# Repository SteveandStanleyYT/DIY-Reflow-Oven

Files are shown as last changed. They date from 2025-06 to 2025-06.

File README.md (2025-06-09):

# DIY Reflow Oven
## Objective
We are going to be building a lot of SMD PCBs in the future and so we would want to invest in a reflow oven. But the current consumer reflow ovens are very expensive and also require a lot of mods to get them working well. For these reasons, we decided to build our own reflow oven. 

## Requirements
- It should be able to fit a medium-sized board.
- It should look aesthetically pleasing (Wires should not be dangling around.)

## Components
| Component | Link | 
|---|---|
| Hamilton Beach toaster oven | [Link](https://www.amazon.com/gp/product/B08CW95ZFR/ref=ewc_pr_img_1?smid=ATVPDKIKX0DER&psc=1) | 
| Panasonic Solid State relay (AQA211VL) | [AQA211VL](https://www.digikey.com/en/products/detail/panasonic-electric-works/AQA211VL/2364682) | 
| RTD PT100 Sensor | [Link](https://www.amazon.com/T-PRO-Bonded-PT100-Sensor-3-3Ft/dp/B08LM65RR9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) |  
| MAX31865 RTD Temperature Thermocouple | [Link](https://www.amazon.com/HiLetgo-MAX31865-Temperature-Thermocouple-Amplifier/dp/B071DVVZHC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) |
| Ceramic Blanket | [Link](https://www.aliexpress.us/item/3256802930270704.html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) | 
| Aluminum reflective tape | — | 
| 240×320 SPI Display | — | 
| ESP32 | — | 
| 12V 1A Power Supply | [Link](https://www.aliexpress.us/item/3256802541723599.html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) | 
| Cooling Fan | — | 
| Green LED | [Link](https://www.digikey.com/en/products/detail/lumex-opto-components-inc/SSI-LXH1090GD/144696)| 
| Red LED | [Link](https://www.digikey.com/en/products/detail/lumex-opto-components-inc/SSI-LXH1090SRD/144702)| 
| Buzzer | — |
| Switch | — | 
| Relay | — |
| Terminal Blocks | — | 
| USB-C to Micro USB cable | - |

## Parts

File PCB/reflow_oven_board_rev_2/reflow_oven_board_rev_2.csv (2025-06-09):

Source: | /Users/stevenketiah/Desktop/Personal_Projects/DIY REFLOW OVEN/Reflow_oven_board/Reflow_oven_board.kicad_sch
Date: | Wednesday, March 13, 2024 at 11:47:50 PM
Tool: | Eeschema 7.0.10
Generator: | /Applications/KiCad/KiCad.app/Contents/SharedSupport/plugins/bom_csv_grouped_by_value.py
Component Count: | 44
Collated Components:
Item | Qty | Reference(s) | Value | LibPart | Footprint | Datasheet | DNP | Availability | Check_prices | Description | MANUFACTURER | MAXIMUM_PACKAGE_HEIGHT | MF | MP | PARTREV | Package | Price | STANDARD | SnapEDA_Link
1 | 1 | BZ1 | Buzzer | Device:Buzzer | Buzzer_Beeper:Buzzer_12x9.5RM7.6 | ~
2 | 1 | C1 | 10u | Device:C | Capacitor_SMD:C_0603_1608Metric_Pad1.08x0.95mm_HandSolder | ~
3 | 3 | C2, C3, C7 | 0.1u | Device:C | Capacitor_SMD:C_0603_1608Metric_Pad1.08x0.95mm_HandSolder | ~
4 | 2 | C4, C5 | 22u | Device:C | Capacitor_SMD:C_0603_1608Metric_Pad1.08x0.95mm_HandSolder | ~
5 | 1 | C6 | 56p | Device:C | Capacitor_SMD:C_0603_1608Metric_Pad1.08x0.95mm_HandSolder | ~
6 | 1 | C8 | 10nF | Device:C | Capacitor_SMD:C_0603_1608Metric_Pad1.08x0.95mm_HandSolder | ~
7 | 1 | J1 | ~ | Connector:Conn_01x14_Socket | Connector_PinSocket_2.54mm:PinSocket_1x14_P2.54mm_Vertical | ~
8 | 6 | J2, J3, J4, J5, J6, J7 | ~ | Connector:Screw_Terminal_01x02 | TerminalBlock_Phoenix:TerminalBlock_Phoenix_MKDS-1,5-2_1x02_P5.00mm_Horizontal | ~
9 | 1 | J8 | Screw_Terminal_01x03 | Connector:Screw_Terminal_01x03 | TerminalBlock_Phoenix:TerminalBlock_Phoenix_MKDS-1,5-3_1x03_P5.00mm_Horizontal | ~
10 | 1 | L1 | 15u | Device:L | Inductor_SMD:L_Taiyo-Yuden_NR-80xx_HandSoldering | ~
11 | 5 | Q1, Q2, Q3, Q4, Q5 | DMG3402L | Transistor_FET:DMG3402L | Package_TO_SOT_SMD:SOT-23 | http://www.diodes.com/assets/Datasheets/DMG3402L.pdf
12 | 1 | R1 | 510k | Device:R_US | Resistor_SMD:R_0603_1608Metric_Pad0.98x0.95mm_HandSolder | ~
13 | 5 | R2, R5, R6, R7, R14 | 150 | Device:R_US | Resistor_SMD:R_0603_1608Metric_Pad0.98x0.95mm_HandSolder | ~
14 | 1 | R3 | 100k | Device:R_US | Resistor_SMD:R_0603_1608Metric_Pad0.98x0.95mm_HandSolder | ~
15 | 1 | R4 | 22.1k | Device:R_US | Resistor_SMD:R_0603_1608Metric_Pad0.98x0.95mm_HandSolder | ~
16 | 2 | R8, R9 | 60.4 | Device:R_US | Resistor_SMD:R_0603_1608Metric_Pad0.98x0.95mm_HandSolder | ~
17 | 5 | R10, R11, R12, R13, R15 | 10k | Device:R_US | Resistor_SMD:R_0603_1608Metric_Pad0.98x0.95mm_HandSolder | ~
18 | 3 | TP1, TP3, TP4 | TestPoint_Alt | Connector:TestPoint_Alt | TestPoint:TestPoint_Pad_D1.0mm | ~
19 | 1 | U1 | ESP32-DEVKIT-V1 | ESP32-DEVKIT-V1:ESP32-DEVKIT-V1 | ESP32-DEVKIT-V1:MODULE_ESP32_DEVKIT_V1 |  |  | Not in stock | https://www.snapeda.com/parts/ESP32-DEVKIT-V1/Do+it/view-part/?ref=eda | Dual core, Wi-Fi: 2.4 GHz up to 150 Mbits/s,BLE (Bluetooth Low Energy) and legacy Bluetooth, 32 bits, Up to 240 MHz | DOIT | 6.8 mm | Do it | ESP32-DEVKIT-V1 | N/A | None | None | Manufacturer Recommendations | https://www.snapeda.com/parts/ESP32-DEVKIT-V1/Do+it/view-part/?ref=snap
20 | 1 | U2 | TPS54202HDDCR | Regulator_Switching:TPS54202H | Package_TO_SOT_SMD:SOT-23-6_Handsoldering | https://www.ti.com/general/docs/suppproductinfo.tsp?distId=10
21 | 1 | U3 | MAX31855KASA | Sensor_Temperature:MAX31855KASA | Package_SO:SOIC-8_3.9x4.9mm_P1.27mm | http://datasheets.maximintegrated.com/en/ds/MAX31855.pdf

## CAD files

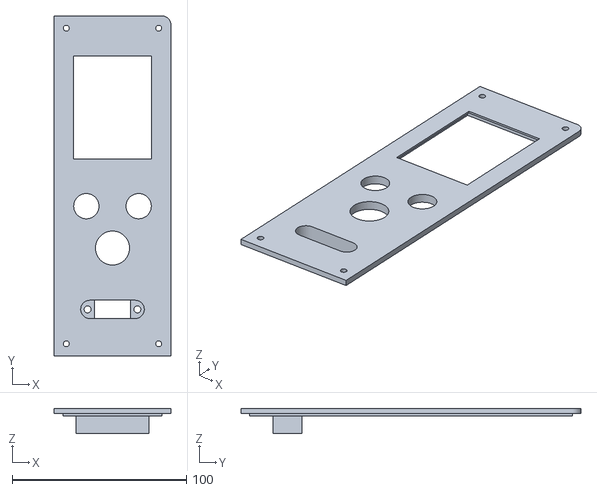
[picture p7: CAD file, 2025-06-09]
CAD/faceplate.stl
67.0 x 195.0 x 14.5

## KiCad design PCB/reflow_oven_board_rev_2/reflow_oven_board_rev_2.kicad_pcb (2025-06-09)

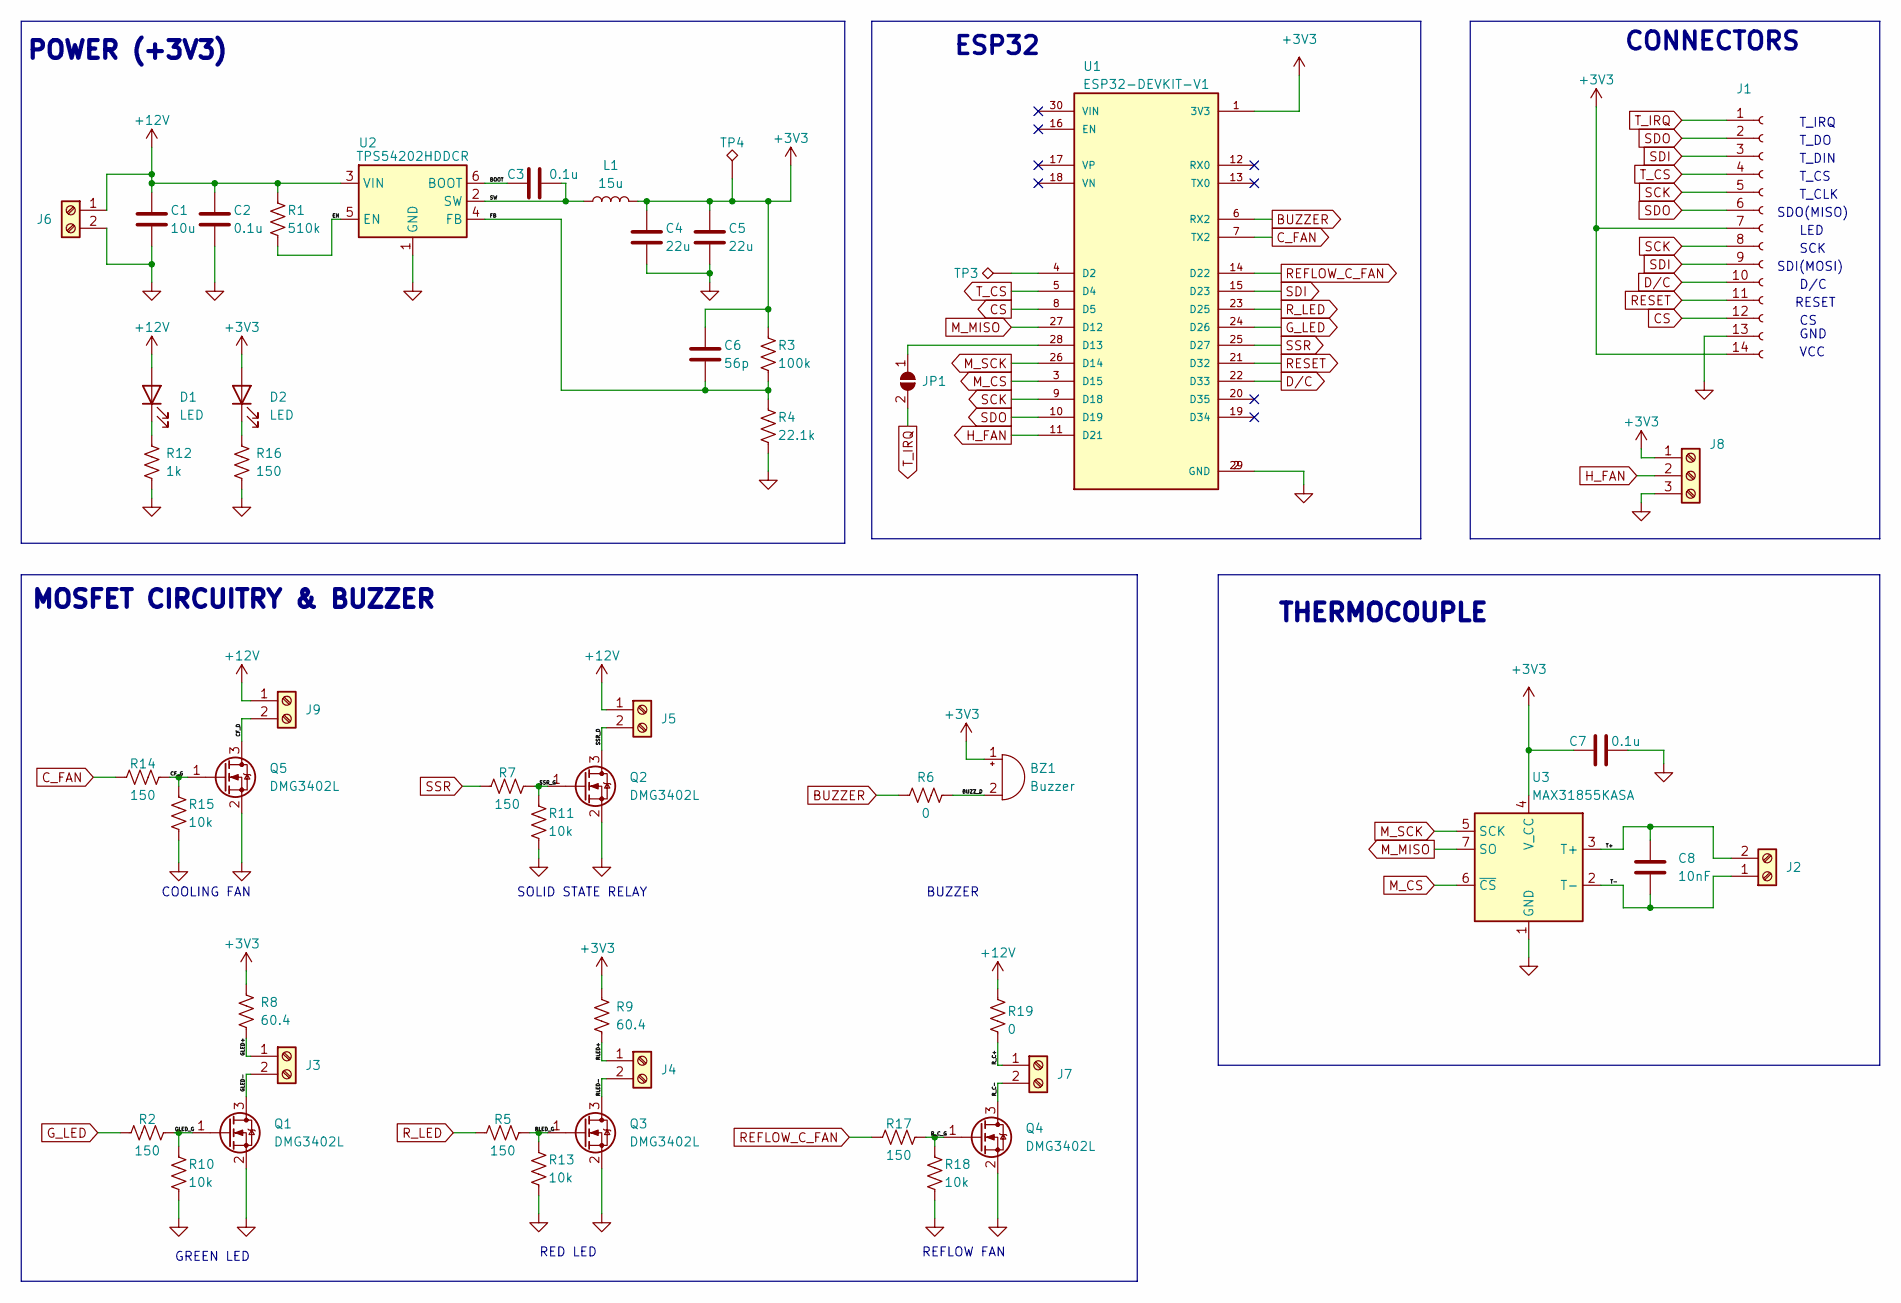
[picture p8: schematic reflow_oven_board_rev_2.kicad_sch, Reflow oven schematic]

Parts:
BZ1: Buzzer; Buzzer_12x9.5RM7.6
C1: 10u; C_0603_1608Metric_Pad1.08x0.95mm_HandSolder
C2, C3, C7: 0.1u; C_0603_1608Metric_Pad1.08x0.95mm_HandSolder
C4, C5: 22u; C_0603_1608Metric_Pad1.08x0.95mm_HandSolder
C6: 56p; C_0603_1608Metric_Pad1.08x0.95mm_HandSolder
C8: 10nF; C_0603_1608Metric_Pad1.08x0.95mm_HandSolder
D1, D2: LED; LED_0603_1608Metric
J1: PinSocket_1x14_P2.54mm_Vertical
J2, J3, J4, J5, J6, J7, J9: TerminalBlock_Phoenix_MKDS-1,5-2_1x02_P5.00mm_Horizontal
J8: Screw_Terminal_01x03; TerminalBlock_Phoenix_MKDS-1,5-3_1x03_P5.00mm_Horizontal
JP1: SolderJumper_2_Open; PinHeader_1x02_P2.54mm_Vertical
L1: 15u; L_Taiyo-Yuden_NR-80xx
Q1, Q2, Q3, Q4, Q5: DMG3402L; SOT-23
R1: 510k; R_0603_1608Metric_Pad0.98x0.95mm_HandSolder
R2, R5, R7, R14, R17: 150; R_0603_1608Metric_Pad0.98x0.95mm_HandSolder
R3: 100k; R_0603_1608Metric_Pad0.98x0.95mm_HandSolder
R4: 22.1k; R_0603_1608Metric_Pad0.98x0.95mm_HandSolder
R6: 0; R_0603_1608Metric
R8, R9: 60.4; R_0603_1608Metric_Pad0.98x0.95mm_HandSolder
R10, R11, R13, R15, R18: 10k; R_0603_1608Metric_Pad0.98x0.95mm_HandSolder
R12: 1k; R_0603_1608Metric
R16: 150; R_0603_1608Metric
R19: 0; R_0603_1608Metric_Pad0.98x0.95mm_HandSolder
TP3, TP4: TestPoint_Alt; TestPoint_Pad_D1.0mm
U1: ESP32-DEVKIT-V1; MODULE_ESP32_DEVKIT_V1; PARTREV N/A
U2: TPS54202HDDCR; SOT-23-6_Handsoldering
U3: MAX31855KASA; SOIC-8_3.9x4.9mm_P1.27mm

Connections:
+3V3: BZ1.1 (+), C4.1, C5.1, C6.1, C7.1, D2.2 (A), J1.7, J1.14, J8.1, L1.2, R3.1, R8.1, R9.1, TP4.1, U1.1 (3V3), U3.4 (V_CC)
+12V: C1.1, C2.1, D1.2 (A), J5.1, J6.1, J9.1, R1.1, R19.1, U2.3 (VIN)
/BOOT: C3.1, U2.6 (BOOT)
/BUZZ_D: BZ1.2 (-), R6.2
/CF_D: J9.2, Q5.3 (D)
/CF_G: Q5.1 (G), R14.2, R15.1
/EN: R1.2, U2.5 (EN)
/FB: C6.2, R3.2, R4.1, U2.4 (FB)
/GLED+: J3.1, R8.2
/GLED-: J3.2, Q1.3 (D)
/GLED_G: Q1.1 (G), R2.2, R10.1
/RLED+: J4.1, R9.2
/RLED-: J4.2, Q3.3 (D)
/RLED_G: Q3.1 (G), R5.2, R13.1
/R_C+: J7.1, R19.2
/R_C-: J7.2, Q4.3 (D)
/R_C_G: Q4.1 (G), R17.2, R18.1
/SSR_D: J5.2, Q2.3 (D)
/SSR_G: Q2.1 (G), R7.2, R11.1
/SW: C3.2, L1.1, U2.2 (SW)
/T+: C8.1, J2.2, U3.3 (T+)
/T-: C8.2, J2.1, U3.2 (T-)
BUZZER: R6.1, U1.6 (RX2)
CS: J1.12, U1.8 (D5)
C_FAN: R14.1, U1.7 (TX2)
D/C: J1.10, U1.22 (D33)
GND: C1.2, C2.2, C4.2, C5.2, C7.2, J1.13, J6.2, J8.3, Q1.2 (S), Q2.2 (S), Q3.2 (S), Q4.2 (S), Q5.2 (S), R4.2, R10.2, R11.2, R12.2, R13.2, R15.2, R16.2, R18.2, U1.2 (GND), U1.29 (GND), U2.1 (GND), U3.1 (GND)
G_LED: R2.1, U1.24 (D26)
H_FAN: J8.2, U1.11 (D21)
M_CS: U1.3 (D15), U3.6 (~CS)
M_MISO: U1.27 (D12), U3.7 (SO)
M_SCK: U1.26 (D14), U3.5 (SCK)
unnamed: D1.1 (K), R12.1
unnamed: D2.1 (K), R16.1
unnamed: JP1.1 (A), U1.28 (D13)
unnamed: TP3.1, U1.4 (D2)
REFLOW_C_FAN: R17.1, U1.14 (D22)
RESET: J1.11, U1.21 (D32)
R_LED: R5.1, U1.23 (D25)
SCK: J1.5, J1.8, U1.9 (D18)
SDI: J1.3, J1.9, U1.15 (D23)
SDO: J1.2, J1.6, U1.10 (D19)
SSR: R7.1, U1.25 (D27)
T_CS: J1.4, U1.5 (D4)
T_IRQ: J1.1, JP1.2 (B)

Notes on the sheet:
GREEN LED
T_CS
LED
THERMOCOUPLE
BUZZER
SOLID STATE RELAY
CONNECTORS
SDI(MOSI)
POWER (+3V3)
T_DIN
RED LED
VCC
RESET
MOSFET CIRCUITRY & BUZZER
T_IRQ
COOLING FAN
REFLOW FAN
GND
SDO(MISO)
T_DO
T_CLK
SCK
ESP32
D/C

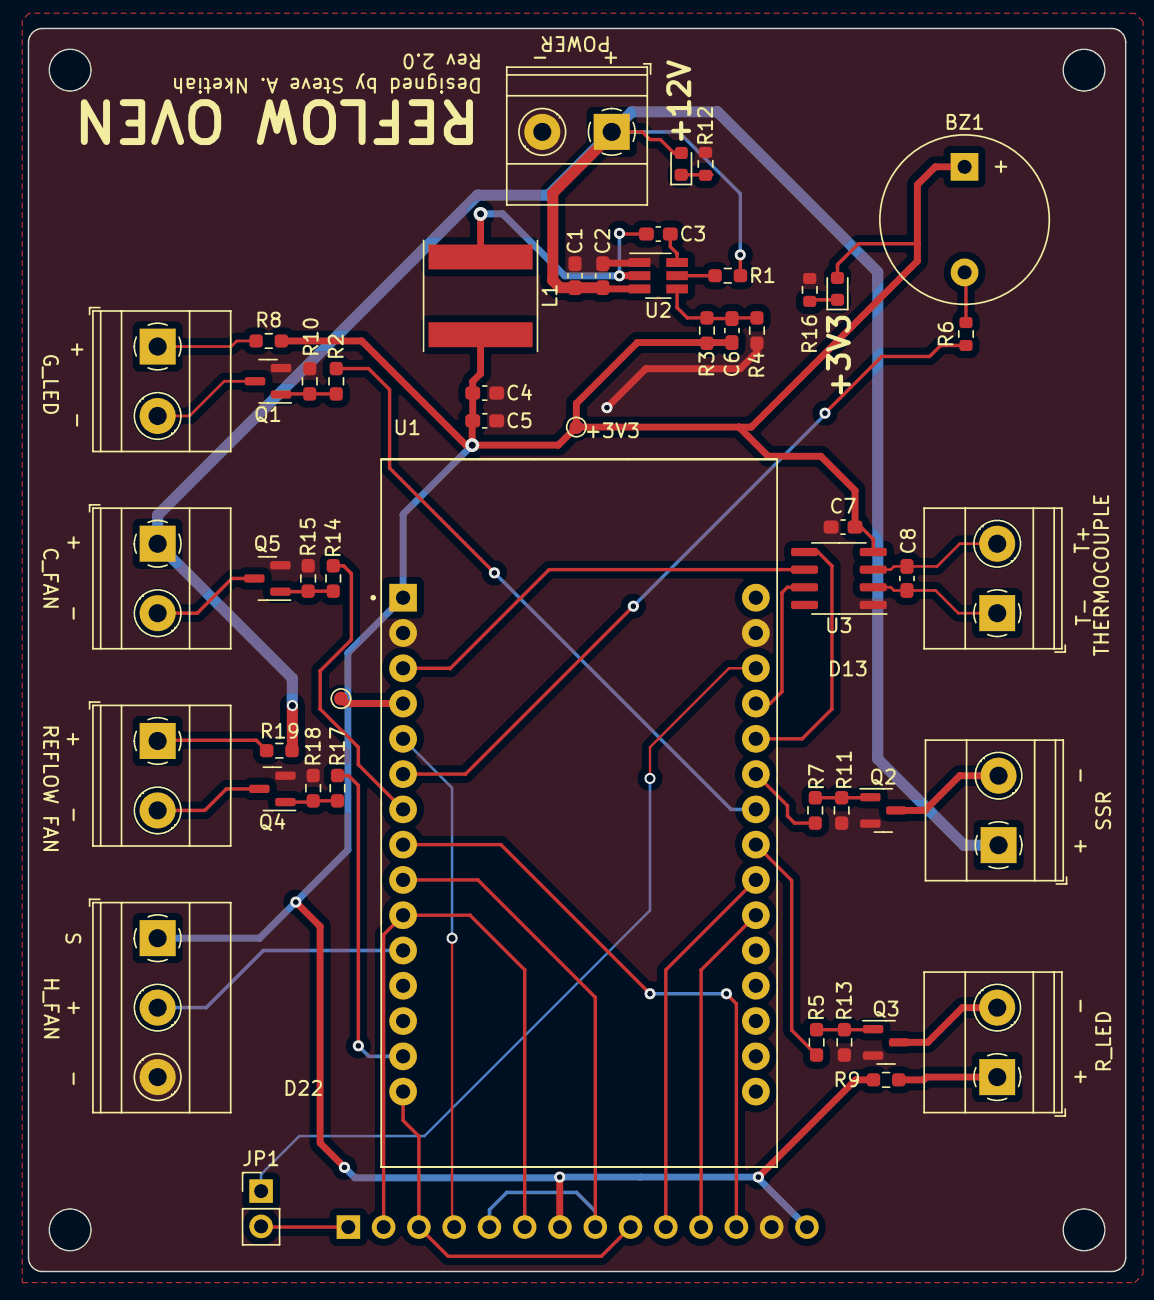
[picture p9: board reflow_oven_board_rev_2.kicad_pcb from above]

Board: 2 copper layers, 79.0 x 89.5 mm, 51 parts (1 on the bottom side), 45 nets.

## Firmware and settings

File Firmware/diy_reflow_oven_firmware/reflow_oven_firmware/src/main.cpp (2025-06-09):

#include <Arduino.h>
#include <TFT_eSPI.h>
#include "GUI.h"
#include "FS.h"

#include "Wire.h"

#include <SPI.h>
#include "Adafruit_MAX31865.h"

#define CALIBRATION_FILE "/TouchCalData1"
#define REPEAT_CAL false


// The value of the Rref resistor. Use 430.0 for PT100 and 4300.0 for PT1000
#define RREF      430.0
// The 'nominal' 0-degrees-C resistance of the sensor
// 100.0 for PT100, 1000.0 for PT1000
#define RNOMINAL  100.0


const int selectPin = 15;
const int dataPin   = 12;
const int clockPin  = 14;

Adafruit_MAX31865 thermo = Adafruit_MAX31865(15, 13, 12, 14);

const int red_led = 25, green_led = 26, ssr = 27, buzzer = 16, cooling_fan = 27, h_fan = 21;

const int SSR_FREQ = 10, ssr_channel = 0, resolution = 8;

int seconds_elapsed = 0, seconds_previous_time = 0; //Keeps track of the seconds elaspsed

void r_led(bool input);
void g_led(bool input);
void PID_control(float s_p);
void heat_fan(bool input);



//PID variables
float PID_p, PID_i, PID_d, set_point, PID_error, PID_prev_error, PID_total;
float kp = 10, kd = 10, ki = 0; 
int refresh_rate = 250;

int ssr_pwm_value;

float current_temp, target_temp;

unsigned long int elapsed_time, previous_time = 0, temperature_time = 0;

//Bake variables
int bake_temp, bake_time, bake_time_left;



// put function declarations here:
void touch_calibrate();

enum Reflow_Mode {
  PREP,
  PREHEAT,
  SOAK,
  REFLOW,
  COOLING
};
enum Reflow_Mode r_mode = PREHEAT;

enum States {
  NONE,
  HOME,
  PROFILES,
  PROFILE_START_SCREEN_1,
  PROFILE_START_SCREEN_LEAD,
  REFLOW_1,
  REFLOW_LEAD,
  DONE,
  BAKE_START_SCREEN,
  BAKE
};
enum States state, prior_state;


TFT_eSPI tft = TFT_eSPI(240,320);
bool pressed;
uint16_t t_x, t_y;

void setup() {
  // put your setup code here, to run once:
  pinMode(red_led, OUTPUT);
  pinMode(green_led, OUTPUT);
  pinMode(ssr, OUTPUT);
  pinMode(buzzer, OUTPUT);
  pinMode(cooling_fan, OUTPUT);
  pinMode(h_fan, OUTPUT);
  ledcSetup(ssr_channel, SSR_FREQ, resolution);
  ledcAttachPin(ssr, ssr_channel);
  Serial.begin(115200);
  tft.init();
  tft.setRotation(0);
  tft.setSwapBytes(true);
  thermo.begin(MAX31865_3WIRE);

  touch_calibrate();

  prior_state = NONE;
  state = HOME;

  Serial.begin(9600);

  digitalWrite(buzzer, HIGH);
}




void loop() {

  //Place get touch cordinate here
  pressed = tft.getTouch(&t_x, &t_y);
  
  
  //Place function that would use the touch inputs to change states here
  if (pressed){
    // tft.setCursor(61, 260, 2);
    // tft.setTextColor(TFT_WHITE,TFT_BLACK, true);  tft.setTextSize(1);
    // tft.print(t_x); tft.print(", "); tft.println(t_y); 
    if (state == HOME){
      if (t_x >= 45 &&  t_x <= 194 && t_y >= 150 && t_y <= 192){         //Profile Button
        state = PROFILES;
      }
      if (t_x >= 45 &&  t_x <= 194 && t_y >= 201 && t_y <= 243){         //Profile Button
        state = BAKE_START_SCREEN;
      }
    }
    
    else if (state == BAKE_START_SCREEN){
      if (t_x >= 9 &&  t_x <= 55 && t_y >= 94 && t_y <= 136){         //Temp - Button
        bake_temp -= 5;
        tft.setTextDatum(TC_DATUM);
        tft.drawString(" " + String(bake_temp) + " " , 120, 107);
      }

      if (t_x >= 182 &&  t_x <= 228 && t_y >= 94 && t_y <= 136){         //Temp + Button
        bake_temp += 5;
        tft.setTextDatum(TC_DATUM);
        tft.drawString(" "  + String(bake_temp) + " " , 120, 107);
      }

      if (t_x >= 9 &&  t_x <= 55 && t_y >= 177 && t_y <= 218){         //Time - Button
        bake_time -= 5;
        tft.setTextDatum(TC_DATUM);
        tft.drawString(" "  +String(bake_time) + " " , 120, 187);
      }
      if (t_x >= 182 &&  t_x <= 228 && t_y >= 177 && t_y <= 218){         //Time + Button
        bake_time += 5;
        tft.setTextDatum(TC_DATUM);
        tft.drawString(" " + String(bake_time)+ " " , 120, 187);
      }
      if (t_x >= 129 &&  t_x <= 223 && t_y >= 237 && t_y <= 279){         //START BUTTON
        state = BAKE;
      }
      if (t_x >= 73 &&  t_x <= 110 && t_y >= 237 && t_y <= 279){         //ABORT BUTTON
        state = HOME;
      }
    }

    else if (state == BAKE){
      if (t_x >= 73 &&  t_x <= 166 && t_y >= 237 && t_y <= 279){         //START BUTTON
        state = BAKE_START_SCREEN;
      }
    }

    else if (state == PROFILES){
      if (t_x >= 46 &&  t_x <= 194 && t_y >= 72 && t_y <= 120) {        //Profile 1 Button
        state = PROFILE_START_SCREEN_1;
      }

      if (t_x >= 46 &&  t_x <= 194 && t_y >= 140 && t_y <= 188) {        //Profile Lead Button
        state = PROFILE_START_SCREEN_LEAD;
      }

      if (t_x >= 46 &&  t_x <= 194 && t_y >= 213 && t_y <= 254) {       //HOME Button
        state = HOME;
      }
    }

    else if (state == PROFILE_START_SCREEN_1 ){
      if (t_x >= 13 &&  t_x <= 106 && t_y >= 248 && t_y <= 288) {       //ABORT Button
        state = PROFILES;
      }
      if (t_x >= 134 &&  t_x <= 227 && t_y >= 248 && t_y <= 288) {      //START Button
        state = REFLOW_1;
      }

    }

    else if (state == PROFILE_START_SCREEN_LEAD ){
      if (t_x >= 13 &&  t_x <= 106 && t_y >= 248 && t_y <= 288) {       //ABORT Button
        state = PROFILES;
      }
      if (t_x >= 134 &&  t_x <= 227 && t_y >= 248 && t_y <= 288) {      //START Button
        state = REFLOW_LEAD;
      }

    }

    else if (state == REFLOW_1 || state == REFLOW_LEAD){
      if (t_x >= 134 &&  t_x <= 227 && t_y >= 248 && t_y <= 288) {      //ABORT Button
        state = HOME;
      }
      
    }

    else if (state == DONE){
      if (t_x >= 70 &&  t_x <= 168 && t_y >= 248 && t_y <= 288) {      //ABORT Button
        state = HOME;
      }

    }
  }


  elapsed_time = millis();

  switch (state){
    case HOME:
      if (prior_state != state){
        //initializing code
        tft.pushImage(0, 0, 240, 320, home);
        prior_state = state;
        ledcWrite(ssr_channel, 0);
        heat_fan(false);
        g_led(1);
        r_led(0);
        tft.setCursor(134, 262, 0);
        tft.setTextColor(TFT_WHITE,TFT_BLACK, true);  
        tft.setTextSize(2);
        tft.print(current_temp);
        tft.println("  ");
    }
      
    if (elapsed_time - seconds_previous_time > 1000){
        seconds_previous_time = elapsed_time;
        current_temp = thermo.temperature(RNOMINAL, RREF);
        elapsed_time = millis();
        tft.setCursor(134, 262, 0);
        tft.setTextColor(TFT_WHITE,TFT_BLACK, true);  
        tft.print(current_temp);
        tft.println("  ");
    }

      break;

    case BAKE_START_SCREEN:
      if (prior_state != state){
        //initializing code
        ledcWrite(ssr_channel, 0);
        g_led(1);
        ledcDetachPin(red_led);
        heat_fan(false);
        prior_state = state;
        tft.pushImage(0, 0, 240, 320, bake);
        tft.pushImage(17, 238, 93, 40, abort_button);
        bake_temp = 60;
        bake_time = 60;
        bake_time_left = 60;

        tft.setTextDatum(TC_DATUM);
        tft.setTextSize(3);
        tft.drawString(" " + String(bake_temp) + " ", 120, 107);
        tft.drawString(" " + String(bake_time) + " ", 120, 187);

      }


    break;

    case BAKE:
    if (prior_state != state){
        //initializing code
        ledcAttachPin(red_led, ssr_channel);
        heat_fan(true);
        g_led(0);
        prior_state = state;
        bake_time_left = bake_time;
        tft.setTextSize(3);
        tft.fillRect(0, 90, 240, 56, TFT_BLACK);
        tft.fillRect(0, 175, 240, 56, TFT_BLACK);
        tft.fillRect(0, 235, 240, 60, TFT_BLACK);
        tft.pushImage(73, 238, 93, 40, abort_button);
        tft.fillRect(16, 155, 155, 22, TFT_BLACK);
        tft.fillRect(16, 68, 155, 22, TFT_BLACK);
        tft.setCursor(17, 155, 0);
        tft.setTextColor(0x057D,TFT_BLACK, true);  
        tft.setTextSize(2);
        tft.println("TIME LEFT      ");
        tft.setCursor(17, 73, 0);
        tft.println("TEMPERATURE    ");
        seconds_elapsed = 0;
        tft.setTextColor(TFT_WHITE,TFT_BLACK, true);  
    }

    PID_control(bake_temp);

    if (elapsed_time - seconds_previous_time >1000 ){
      bake_time_left = bake_time - seconds_elapsed / 60;
      seconds_previous_time = elapsed_time;
      current_temp = thermo.temperature(RNOMINAL, RREF);
      tft.setTextDatum(TC_DATUM);
      tft.setTextSize(3);
      tft.drawString( " " + String((int)round(current_temp)) + "/" + String(bake_temp) + "c " , 120, 107);
      tft.drawString(" " + String(bake_time_left) + "min ", 120, 187);

      seconds_elapsed++;
    }

    if (bake_time_left == 0){
      state = DONE;
    }



    break;



  case PROFILES:
    if (prior_state != state){
        //initializing code
        tft.pushImage(0, 0, 240, 320, profiles_screen);
        prior_state = state;
        ledcWrite(ssr_channel, 0);
        g_led(1);
        r_led(0);
        heat_fan(false);
      }
      


    break;

  case PROFILE_START_SCREEN_1:
    if (prior_state != state){
        //initializing code
        tft.fillScreen(TFT_BLACK);
        tft.pushImage(0, 0, 240, 58, profile_start_NC191SNL50);
        tft.pushImage(0, 62, 240, 184, profile_1_graph);
        tft.pushImage(0, 246, 240, 74, profile_start_buttons);
        prior_state = state;
        ledcWrite(ssr_channel, 0);
        g_led(1);
        r_led(0);
        heat_fan(false);
      }


    break;

  case REFLOW_1:
    if (prior_state != state){
        //initializing code
        tft.pushImage(0, 245, 240, 46, reflow_buttons);
        prior_state = state;
        ledcAttachPin(red_led, ssr_channel);
        g_led(0);
        heat_fan(false);
        seconds_elapsed = 0;
        
      }

  if (elapsed_time - seconds_previous_time > 1000){

    current_temp = thermo.temperature(RNOMINAL, RREF);
    tft.setCursor(61, 246, 2);
    tft.setTextColor(TFT_WHITE,TFT_BLACK, true);  tft.setTextSize(1);
    tft.println(seconds_elapsed);

    tft.setCursor(61, 260, 2);
    tft.setTextColor(TFT_WHITE,TFT_BLACK, true);  tft.setTextSize(1);
    tft.println(current_temp);

    tft.setCursor(62, 275, 2);
    tft.setTextColor(TFT_WHITE,TFT_BLACK, true);  tft.setTextSize(1);
    if(r_mode == PREHEAT){
      tft.println("PREHEAT   ");
    }
    else if (r_mode == SOAK){
      tft.println("SOAK      ");
    }
    else if(r_mode == REFLOW){
      tft.println("REFLOW    ");
    }
    else if(r_mode == COOLING){
      tft.println("COOLING");
    }



    int pixel_y = round((-1.0/2.0)*current_temp + 214);
    int pixel_x = round((7.0/12.0)*seconds_elapsed + 34);
    tft.drawPixel(pixel_x, pixel_y, TFT_WHITE);


    seconds_elapsed++;
    seconds_previous_time = elapsed_time;

  }

  if (seconds_elapsed <= 90){
    target_temp = (125.00/90.00)*(float)seconds_elapsed + 25;
    r_mode = PREHEAT;
  }
  else if (seconds_elapsed <= 180){
    target_temp = (5.00/18.00)*(float)seconds_elapsed + 125;
    r_mode = SOAK;
  }
  else if (seconds_elapsed <= 240 && current_temp <= 249){
    target_temp = (37.00/30.00)*(float)seconds_elapsed - 47;
    r_mode = REFLOW;
  }
  else if (seconds_elapsed > 240){
    r_mode = COOLING;
  }

  PID_control(target_temp);
  if (seconds_elapsed > 240){
    state = DONE;
  }

  break;

  case PROFILE_START_SCREEN_LEAD:
    if (prior_state != state){
        //initializing code
        tft.fillScreen(TFT_BLACK);
        tft.pushImage(0, 0, 240, 60, Lead_Reflow_title);
        tft.pushImage(0, 62, 240, 184, Lead_Reflow_graph);
        tft.pushImage(0, 246, 240, 74, profile_start_buttons);
        prior_state = state;
        ledcWrite(ssr_channel, 0);
        g_led(1);
        r_led(0);
        heat_fan(false);
      }


    break;

  case REFLOW_LEAD:
    if (prior_state != state){
        //initializing code
        tft.pushImage(0, 245, 240, 46, reflow_buttons);
        prior_state = state;
        ledcAttachPin(red_led, ssr_channel);
        g_led(0);
        heat_fan(false);
        seconds_elapsed = -10;
        r_mode = PREP;
        
      }

  if (elapsed_time - seconds_previous_time > 1000){

    current_temp = thermo.temperature(RNOMINAL, RREF);

    if (r_mode != PREP){
      int pixel_y = round((-1.0/2.0)*current_temp + 214);
      int pixel_x = round((7.0/12.0)*seconds_elapsed + 34);
      tft.drawPixel(pixel_x, pixel_y, TFT_WHITE);

      tft.setCursor(61, 246, 2);
      tft.setTextColor(TFT_WHITE,TFT_BLACK, true);  tft.setTextSize(1);
      tft.println(seconds_elapsed);
    }

    tft.setCursor(61, 260, 2);
    tft.setTextColor(TFT_WHITE,TFT_BLACK, true);  tft.setTextSize(1);
    tft.println(current_temp);

    tft.setCursor(62, 275, 2);
    tft.setTextColor(TFT_WHITE,TFT_BLACK, true);  tft.setTextSize(1);

    if(r_mode == PREP){
      ledcWrite(ssr_channel,255);
      tft.println("PREP      ");
    }
    else if(r_mode == PREHEAT){
      tft.println("PREHEAT   ");
    }
    else if (r_mode == SOAK){
      tft.println("SOAK      ");
    }
    else if(r_mode == REFLOW){
      tft.println("REFLOW    ");
    }
    else if(r_mode == COOLING){
      tft.println("COOLING");
    }


    

    seconds_elapsed++;
    seconds_previous_time = elapsed_time;

  }
  if (seconds_elapsed <= 0){
    r_mode = PREP;
  }

  else if (seconds_elapsed <= 30){
    target_temp = (75.00/30.00)*(float)seconds_elapsed + 25;
    r_mode = PREHEAT;
  }
  else if (seconds_elapsed <= 120){
    target_temp = (5.00/9.00)*(float)seconds_elapsed + 83.33;
    r_mode = SOAK;
  }
  else if (seconds_elapsed <= 210 && current_temp <= 235){
    target_temp = (17.00/18.00)*(float)seconds_elapsed + 110/3;
    r_mode = REFLOW;
  }
  else if (seconds_elapsed > 210){
    r_mode = COOLING;
  }
  if (r_mode != PREP){
    PID_control(target_temp);
  }
  
  if (seconds_elapsed > 210){
    state = DONE;
  }

  break;

  case DONE:
  if (prior_state != state){
      //initializing code
      tft.pushImage(0, 54, 240, 236, done);
      prior_state = state;
      ledcWrite(ssr_channel, 0);
      g_led(1);
      r_led(0);
      heat_fan(true);
      ledcDetachPin(red_led);
      
      current_temp = thermo.temperature(RNOMINAL, RREF);
      tft.setCursor(138, 213, 0);
      tft.setTextColor(TFT_WHITE,TFT_BLACK, true);  tft.setTextSize(2);
      tft.print(current_temp);
      tft.println("   ");  

      tone(buzzer, 2000);
      delay(500);
      noTone(buzzer);
      delay(500);
      current_temp = thermo.temperature(RNOMINAL, RREF);
      tft.setCursor(138, 213, 0);
      tft.setTextColor(TFT_WHITE,TFT_BLACK, true);  tft.setTextSize(2);
      tft.print(current_temp);
      tft.println("   ");
      tone(buzzer, 2000);
      delay(500);
      noTone(buzzer);
      delay(500);
      current_temp = thermo.temperature(RNOMINAL, RREF);
      tft.setCursor(138, 213, 0);
      tft.setTextColor(TFT_WHITE,TFT_BLACK, true);  tft.setTextSize(2);
      tft.print(current_temp);
      tft.println("   ");
      tone(buzzer, 2000);
      delay(500);
      noTone(buzzer);
      delay(500);
      current_temp = thermo.temperature(RNOMINAL, RREF);
      tft.setCursor(138, 213, 0);
      tft.setTextColor(TFT_WHITE,TFT_BLACK, true);  tft.setTextSize(2);
      tft.print(current_temp);
      tft.println("   ");
      tone(buzzer, 2000);
      delay(500);
      noTone(buzzer);
      delay(500);
      current_temp = thermo.temperature(RNOMINAL, RREF);
      tft.setCursor(138, 213, 0);
      tft.setTextColor(TFT_WHITE,TFT_BLACK, true);  tft.setTextSize(2);
      tft.print(current_temp);
      tft.println("   ");
      tone(buzzer, 2000);
      delay(500);
      noTone(buzzer);
      delay(500);
      elapsed_time = millis();
    }
    if (elapsed_time - seconds_previous_time > 1000){
      current_temp = thermo.temperature(RNOMINAL, RREF);
      tft.setCursor(138, 213, 0);
      tft.setTextColor(TFT_WHITE,TFT_BLACK, true);  tft.setTextSize(2);
      tft.print(current_temp);
      tft.println("   ");
      seconds_previous_time = millis();
    }

    break;
  
  }


  delay(10);

  }

// put function definitions here:

void r_led(bool input){
  if (input == true){
    digitalWrite(red_led, HIGH);
  }
  else {
    digitalWrite(red_led, LOW);
  }
}

void g_led(bool input){
  if (input == true){
    digitalWrite(green_led, HIGH);
  }
  else {
    digitalWrite(green_led, LOW);
  }
}

void heat_fan(bool input){
  if (input == true){
    digitalWrite(h_fan, HIGH);
  }
  else {
    digitalWrite(h_fan, LOW);
  }
}

void PID_control(float s_p){
  set_point = s_p;
  if((elapsed_time - previous_time) > refresh_rate){
    
    PID_error = set_point - current_temp;
    PID_p = kp*PID_error;
    PID_d = kd*((PID_error - PID_prev_error)/refresh_rate);

    PID_total = PID_p - PID_d;

    PID_total = map(PID_total, 0, 50 , 0, 255);
    
    if (PID_total > 255){
      PID_total = 255;
    }
    else if (PID_total < 0){
      PID_total = 0;
    }

    ledcWrite(ssr_channel, (int)PID_total);

    PID_prev_error = PID_error;
    previous_time = millis();
    
  }
  
}




void touch_calibrate()
{
  uint16_t calData[5];
  uint8_t calDataOK = 0;

  // check file system exists
  if (!SPIFFS.begin()) {
    Serial.println("formatting file system");
    SPIFFS.format();
    SPIFFS.begin();
  }

  // check if calibration file exists and size is correct
  if (SPIFFS.exists(CALIBRATION_FILE)) {
    if (REPEAT_CAL)
    {
      // Delete if we want to re-calibrate
      SPIFFS.remove(CALIBRATION_FILE);
    }
    else
    {
      fs::File f = SPIFFS.open(CALIBRATION_FILE, "r");
      if (f) {
        if (f.readBytes((char *)calData, 14) == 14)
          calDataOK = 1;
        f.close();
      }
    }
  }

  if (calDataOK && !REPEAT_CAL) {
    // calibration data valid
    tft.setTouch(calData);
  } else {
    // data not valid so recalibrate
    tft.fillScreen(TFT_BLACK);
    tft.setCursor(20, 0);
    tft.setTextFont(2);
    tft.setTextSize(1);
    tft.setTextColor(TFT_WHITE, TFT_BLACK);

    tft.println("Touch corners as indicated");

    tft.setTextFont(1);
    tft.println();

    if (REPEAT_CAL) {
      tft.setTextColor(TFT_RED, TFT_BLACK);
      tft.println("Set REPEAT_CAL to false to stop this running again!");
    }

    tft.calibrateTouch(calData, TFT_MAGENTA, TFT_BLACK, 15);

    tft.setTextColor(TFT_GREEN, TFT_BLACK);
    tft.println("Calibration complete!");

    // store data
    fs::File f = SPIFFS.open(CALIBRATION_FILE, "w");
    if (f) {
      f.write((const unsigned char *)calData, 14);
      f.close();
    }
  }
}
